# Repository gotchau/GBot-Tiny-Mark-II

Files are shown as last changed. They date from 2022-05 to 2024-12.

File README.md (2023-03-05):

# GBot-Tiny-Mark-II

<a href="https://discord.gg/KYU2nGtZ2r" style="height: 40px !important;">Join us on Discord</a>

Это вторая версия моего первого принтера GBot Tiny. Новый принтер теперь чуточку компактней по XY, но выше, при этом зона печати стала слегка больше.  

> [Список комплектующих для постройки принтера.](./docs/BOM_GBot_Tiny_Mark_II.md)

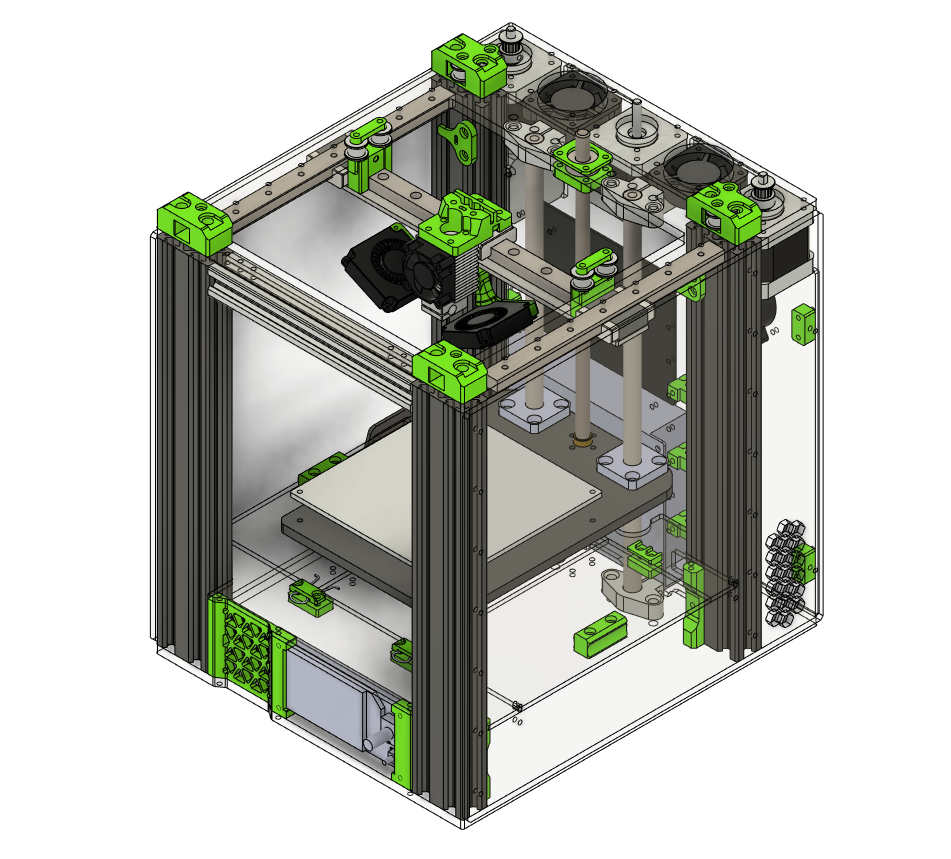
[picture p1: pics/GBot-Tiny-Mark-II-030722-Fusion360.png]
Внешний вид принтер


## Обзор конструкции
Рама теперь состоит из профиля 2040. Из-за того, что рама стала меньше, она стала жёстче. Первая версия не имела отсека под электронику, новая - целых два (легкодоступный под столиком и сзади). Материнскую плату и блок питания предполагается ставить сзади. Таким образом можно добиться максимально компактной компоновки и "подключать движки проводами 10см". Я для себя буду собирать принтер на клиппере, поэтому в переднем отсеке прекрасно разместится одноплатный компьютер со своим блоком питания или понижающим преобразователем.

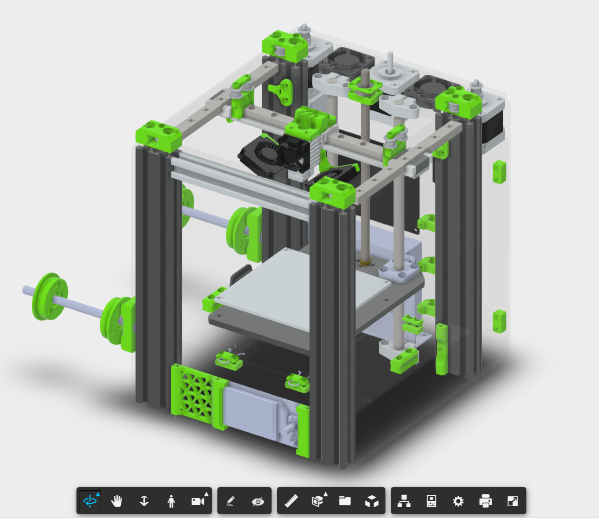
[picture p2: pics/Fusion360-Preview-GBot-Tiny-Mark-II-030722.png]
Preview (https://myhub.autodesk360.com/ue2ddbd59/shares/public/SH35dfcQT936092f0e43e492bbc572dd28c1?mode=embed)


> https://myhub.autodesk360.com/ue2ddbd59/g/shares/SH35dfcQT936092f0e43e492bbc572dd28c1?mode=embed

## Что изменилось?

- Рама стала жёстче
- Занимает меньше места на столе

- Появились отсеки для электроники (я говорил, что их два?)
- Каретки рельс не выходят за границы корпуса => корпус можно накрыть куполом и сделать пассивную термокамеру
- Концевики на датчиках Холла [А3144](./docs/Datasheet_A3144.pdf)
- Появилось нормальное крепление экрана (совмещено с подвальчиком)
- Появился подвальчик, доступ к которому есть сверху (принтер не требуется переворачивать)
- Катушка пластика меняется сверху, это позволяет ставить принтеры вплотную друг к другу
- Верхняя и нижняя плиты стали проще по геометрии, теоретически можно вырезать кустарно
- Рюкзак *aka* backpack/задний отсек имеет активное охлаждение (два осевых 4010, радиальный 4020)

## Примечание
В папке [CAD] вы найдёте актуальные модели для производства данного принтера. [DXF] - для лазерной резки, [STL] - для печати. В этих папках лежат детали с минимальным риском изменения. Остальные детали всегда можно взять из актуальной step-сборки принтера из папки [STEP].

Вся документация и вспомогательные файлы будут находиться здесь [docs].

[CAD]: ./CAD
[docs]: ./docs
[DXF]: ./CAD/Tiny%20Mark%20II/DXF
[STL]: ./CAD/Tiny%20Mark%20II/STL
[STEP]: ./CAD/Tiny%20Mark%20II/STEP

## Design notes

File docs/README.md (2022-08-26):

## Содержание данной секции:

**[BOM GBot Tiny Mark II.md](BOM_GBot_Tiny_Mark_II.md)** — список комплектующих

**[Fixings BOM GBot Tiny Mark II.md](Fixings_BOM_GBot_Tiny_Mark_II.md)** — расширенный список "болтов, винтов и гаек"

**[Datasheet A3144.pdf](Datasheet_A3144.pdf)** — документация на датчики Холла А3144, которые используются как концевики

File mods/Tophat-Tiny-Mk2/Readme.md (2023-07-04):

# Купол Tiny Mark II

## Внешний вид

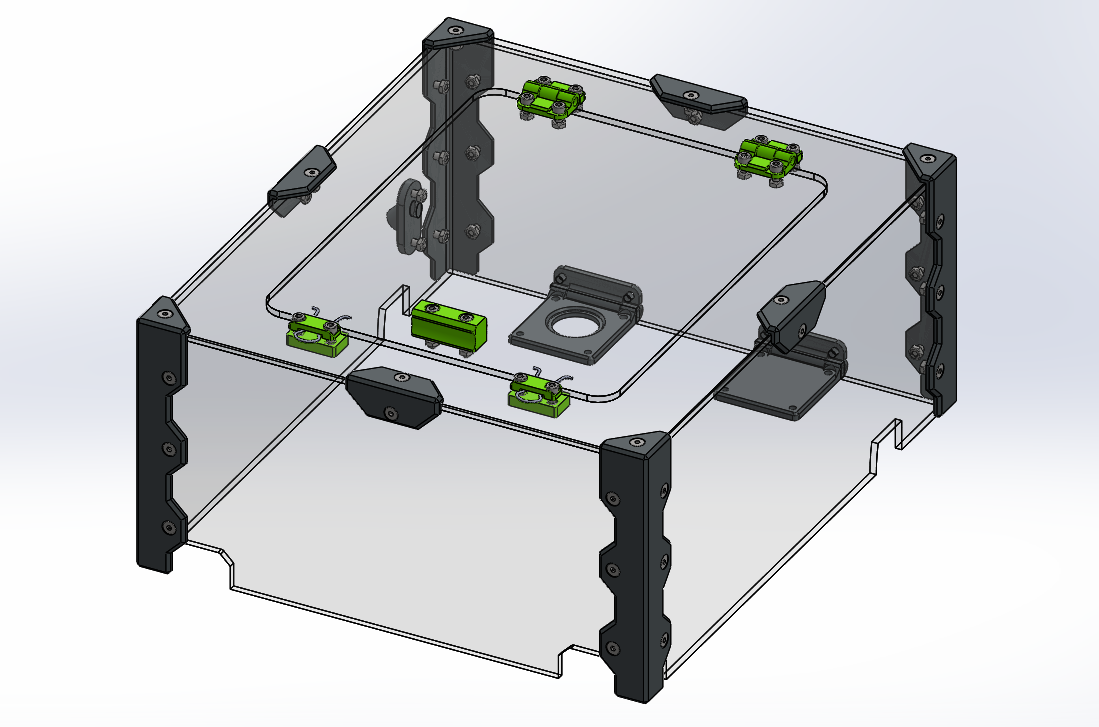
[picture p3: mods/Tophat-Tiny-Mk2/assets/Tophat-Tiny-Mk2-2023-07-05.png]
купол


Купол состоит из 5 панелей вырезанных из акрила 3мм, которые скрепляются с помощью печатных уголков. Пруток с пластиком заводится во внутрь по боудену через штуцер на боковой стенке. Жгут проводов до печатной головы идёт сквозь отверстие одной из петель. Спроектировано под разъем GX20. Петли крепятся на места вентиляторов отсека электроники. Отказ от них не критичен. У меня отсек работает всегда в пассивном режиме. 

Файлы STL и DXF находятся в соответствующих папках.

В папке **assets** есть несколько видео того, как это выглядит уже в собранном виде.

## Благодарности

Данный купол появился на свет благодаря активности сообщества. Большое спасибо Алексею.

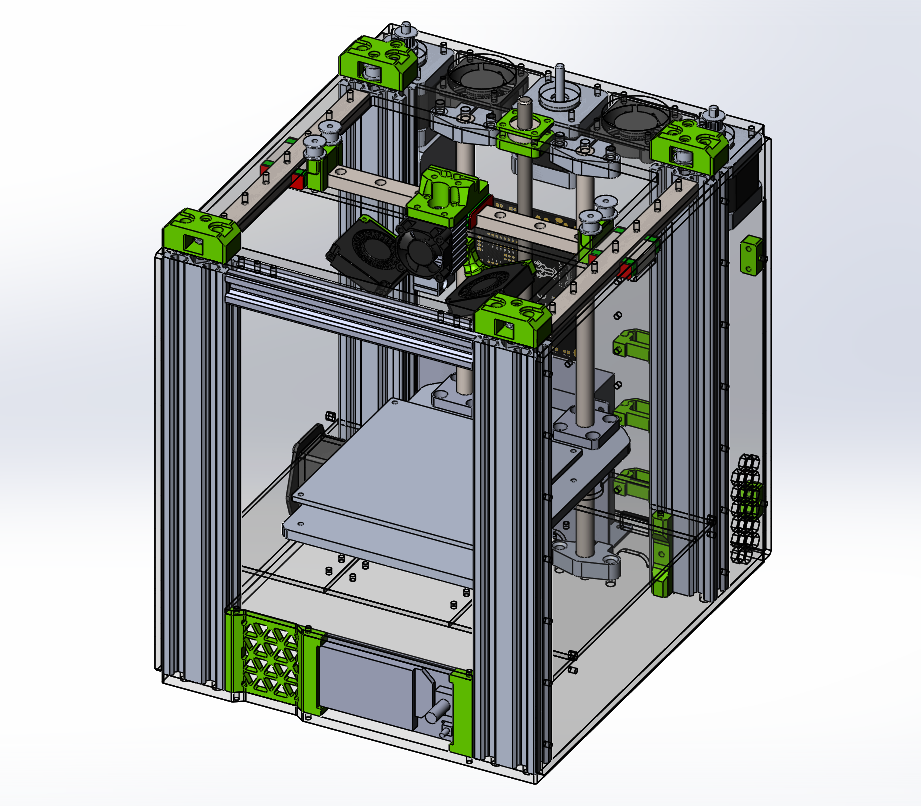
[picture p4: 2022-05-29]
pics/GBot-Tiny-Mark-II-290522.png

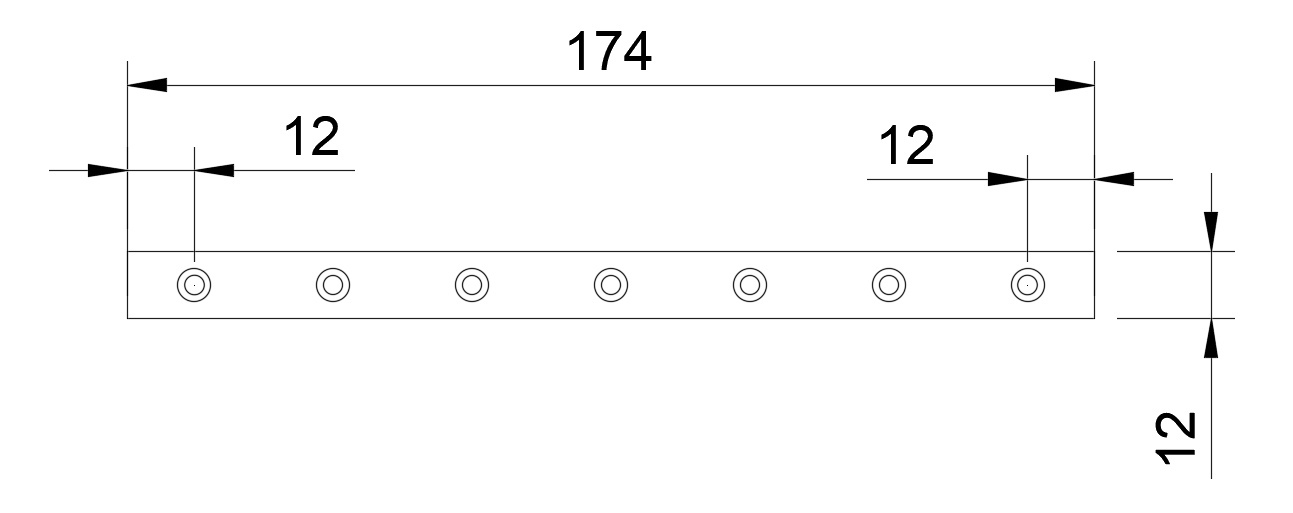
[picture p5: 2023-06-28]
docs/drawings/Y_Rail_GBot_Tiny_Mk2.jpg

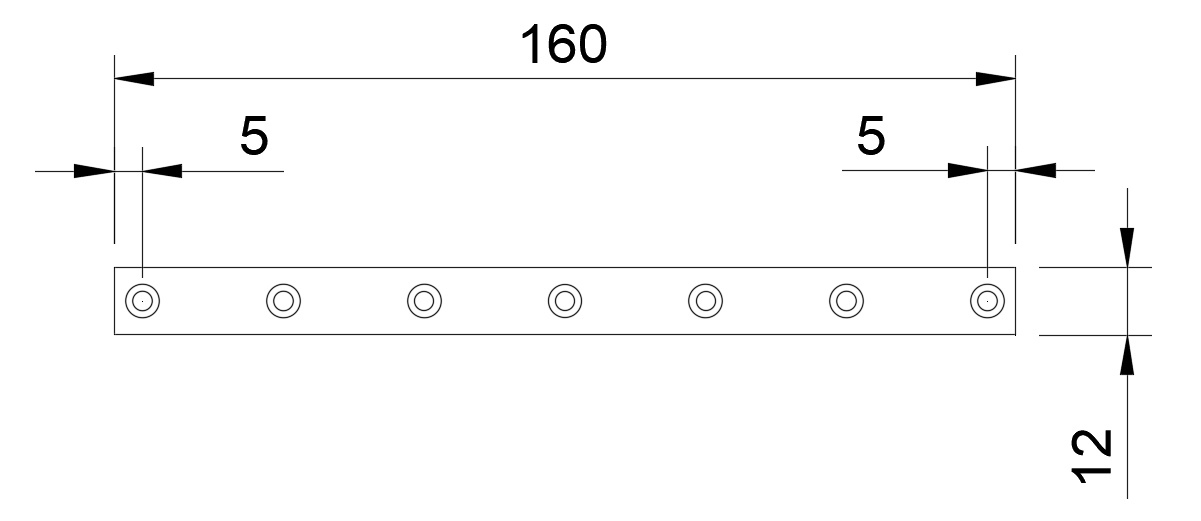
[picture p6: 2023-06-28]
docs/drawings/X_Rail_GBot_Tiny_Mk2.jpg

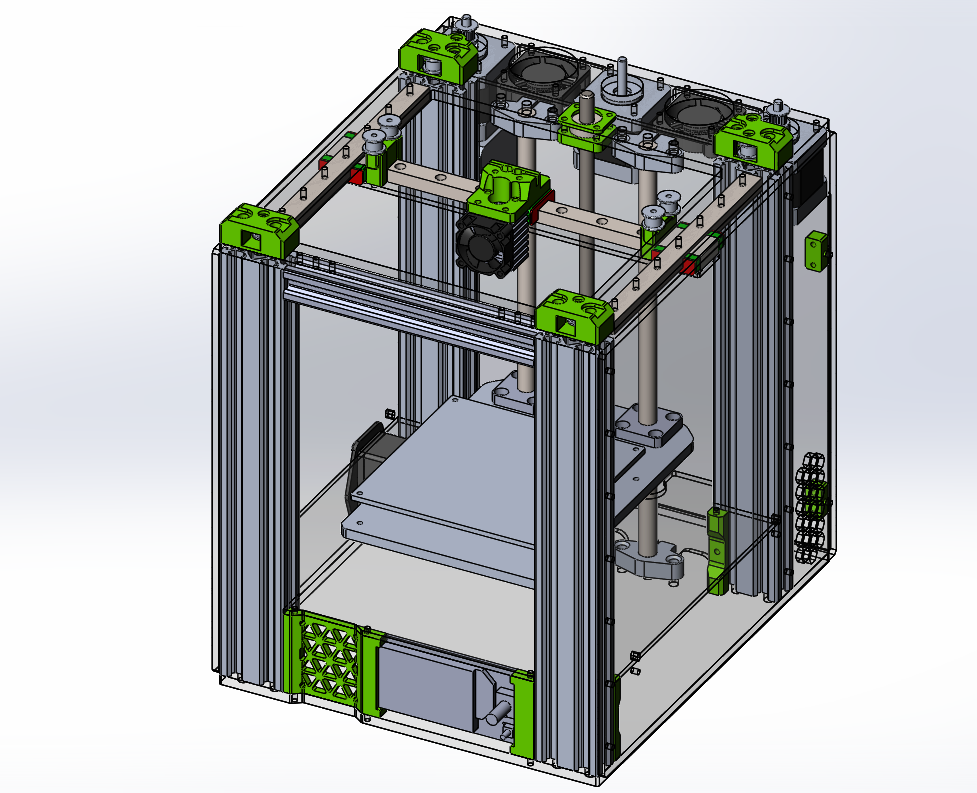
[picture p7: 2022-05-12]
pics/GBot-Tiny-Mark-II-120522.png

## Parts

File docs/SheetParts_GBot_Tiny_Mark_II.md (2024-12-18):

# Список листовых деталей

Несколько наименований в одной ячейке означает, что у детали есть несколько вариантов исполнения. Изготовить необходимо только одну.

## Акриловые детали для корпуса

| Название | Толщина | Количество | Комментарий |
| --- | :-----: | :---: | --- |
| topPlate GBtTinyMII.DXF |  6 мм | 1 | |
| bottomPlate GBtTinyMII.DXF<br/>bottomPlate 10mm GBtTinyMII.DXF |  6 мм | 1 | `bottomPlate 10mm` – отверстия для сквозной установки валов Z |
| leftPanel GBtTinyMII.DXF |  3 мм | 1 | |
| rightPanel GBtTinyMII.DXF |  3 мм | 1 | |
| electronicsCover GBtTinyMII.DXF |  3 мм | 1 | Комбинированная деталь<br/>Есть возможность вырезать по отдельности, детали с пометкой `(optional)`<br/>[Подробнее ниже](#electronicsCover-по-частям) |
| backPanel GBtTinyMII.DXF |  3 мм | 1 | |
| backBackPanel GBtTinyMII.DXF |  3 мм | 1 | |
| xRailSupport GBtTinyMII.DXF |  3 мм | 1 | |
| frontDoor GBtTinyMII.DXF | 3мм | 1 | Дверца (опция) |

## Прочие листовые детали

### Крепление стола

В таблице ниже представлено несколько вариаций крепления столика. Изготовить нужно только одну. Различия указаны в столбце комментарий.

Крепление стола по трём точкам предпочтительней. Если не знаете, что выбрать, берите `bedMount GBtTinyMII.DXF`. Материал сталь 4мм.

| Название | Толщина | Количество | Комментарий |
| --- | :-----: | :---: | --- |
| bedMount GBtTinyMII.DXF |  4 мм | 1 | Отверстия 3.5 мм под резьбу или рассверливание<br />Поддерживает крепление столика по 3 и 4 точкам |
| bedMount BH4 GBtTinyMII.DXF |  4 мм | 1 | Отверстия 4 мм сразу под винты М4<br />Поддерживает крепление столика по 3 и 4 точкам |
| bedMountThreePoint GBtTinyMII.DXF |  4 мм | 1 | Поддерживает крепление столика только 3 точкам |

### Пластина стола

Применяется для самостоятельной сборки столика, если его не удалось купить в сборе, так как с момента выхода принтера наблюдается дефицит столов 120мм. Снизу крепится грелка 100мм. Материал алюминий.

| Название | Толщина | Количество | Комментарий |
| --- | :-----: | :---: | --- |
| realHotBed 120x120mm.DXF |  3 мм | 1 | Поддерживает крепление по 3 и 4 точкам |

## electronicsCover по частям

Если вдруг материала не хватает, то electronicsCover можно вырезать частями.

| Название | Толщина | Количество | Комментарий |
| --- | :-----: | :---: | --- |
| (optional) back electronicsCover GBtTinyMII.DXF |  3 мм | 1 | |
| (optional) center electronicsCover GBtTinyMII.DXF |  3 мм | 1 | |
| (optional) front electronicsCover GBtTinyMII.DXF |  3 мм | 1 | |
| (optional) leftRight electronicsCover GBtTinyMII.DXF |  3 мм | 2 | |

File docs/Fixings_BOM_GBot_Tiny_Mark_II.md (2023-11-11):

# Список крепежа GBot Tiny Mark II

| Что | Сколько | Для чего | Комментарий |
| --- | --- | --- | --- |
| **Стенки** | | | |
| M3x8 | от 4 до 14 штук | Левая стенка | |
| M3x8 | от 4 до 14 штук | Правая стенка | |
| | | | |
| **Верхняя и нижняя пластины** | | | |
| M6x30 | 8 штук | Верхняя пластина | Силовые; DIN 912 |
| M6x20 | 8 штуки | Нижняя пластина | Силовые; DIN 912 |
| M3x12 | от 6 до 14 штук | Рельсы Y | |
| M3x12..18 | 6 штук | Холостые шкивы по периметру | |
| M3x20 | 8 штук | Вентиляторы заднего отсека | |
| M3x10 | 12 штук | Двигатели ABZ | |
| M3x12 | 4 штуки | Подшипник Z | |
| | | | |
| **Ось X** | | | |
| M3x40 | 4 штуки | Шкивы на оси Х | Рекомендуется винт с широкой шляпкой/фланцем;<br />DIN 967 или 7380-2 |
| M3x12 | 2 штуки | Флажок концевика Y | |
| M3x6 | 6 штук | Крепление поддержки рельсы оси Х | |
| M3x10 | от 3 до 7 штук  | Рельса оси Х | |
| | | | |
| **Ось Z** | | | |
| M5x20 | 8 штук | Валы оси Z | если валы с резьбой, то 4 штуки;<br />DIN 912 или DIN 7420 |
| M3x12 | 4 штуки | Латунная гайка | |
| M4x10 | 8 штук | Линейные подшипники | DIN 912 |
| | | | |
| **Печатная головка** | | | |
| M3x8 | 2 штуки | Крепление к каретке оси Х | |
| M3x18 | 2 штуки | Крепление к каретке оси Х | |
| M3x12 | 2 штуки | Крепление ремня | |
| M3x12 | 4 штуки | Крепление радиатора | |
| M3x16 | 2 штуки | Обдув модели | |
| M2x6..8 | 4 штуки | Обдув модели | |
| | | | |
| **Подвальчик** | | | |
| M3x16 | 4 штуки | Ручки крышки подвала | |
| M3x12 | 16 штук | Петли крышки подвала | |
| M3x12 | 8 штук | Защёлки/ответная часть | |
| M3x10 | 8 штук | Крепление к раме | |
| M3x10..20 | 6 штук | Крепление экрана | |
| M3x4 | 4 штуки | Крепление экрана | |
| M3x10 | 2 штуки | Гнездо питания | Рекомендуется DIN 965 |
| | | | |
| **Задний отсек электроники / рюкзак / backpack** | | | |
| M3x10 | 3 штуки | Блок питания | |
| M3x8 | 4 штуки | Шайбы упоры задней стенки электроники | |
| M3x12 | 9 штук | Крепление задней крышки | |
| M3x8 | 6 штук | Органайзер (если ставить 3 штуки) | |
| M3x8 | 8 штук | Крепление управляющей платы | Пластмассовые стойки |
| M3x8 | 4 штуки | Крепление управляющей платы | Пластмассовые винты |
| M3x8 | 4 штуки | Концевики YZ | |

*для большинства крепежа стоит брать DIN 7985 или 7380, если в таблице не указано иное

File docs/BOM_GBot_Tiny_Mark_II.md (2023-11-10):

# Список комплектующих GBot Tiny Mark II

### Железо

| Наименование | Количество | Ссылка | Комментарий |
| --- | :---: | --- | --- |
| Комплект шаговых двигателей | 1 | http://got.by/6eac1e | Всего требуется 4 двигателя<br />3 двигателя, если на директе |
| Рельс с кареткой MGN12C | 3 | http://got.by/6eac2d | Берём 200мм; Две для Y режутся в 174мм, одна для X 160мм |
| Блок питания Mean Well LRS-150-24 | 1 | http://got.by/6eac2y | |
| Печатающая головка | 1 | http://got.by/6eac44 | |
| Подающий механизм | 1 | http://got.by/6eac5o | В оригинале левое исполнение, но есть возможность собрать зеркально (с правым) |
| Вал 10мм (комплект из 2 шт) | 1 | http://got.by/6eac6u | Диаметр 10мм длина 300мм, режется в 270мм |
| Держатель вала SHF10 (комплект 4шт) | 1 | https://alii.pub/6lk0tg<br />https://alii.pub/6lk0v7 | |
| Линейный подшипник LMK10UU | 2 | http://got.by/6eacax | UU - короткий, LUU - длинный; нам нужен короткий |
| Шкивы на двигатели XY (16 зубов) | 2 | http://got.by/6eacca | 16 teeth bore 5 |
| Шкив на двигатель Z (20 зубов) | 1 | http://got.by/6eacca | 20 teeth bore 5 |
| Шкив на винт оси Z (20 зубов) | 1 | http://got.by/6eacca | 20 teeth bore 8 |
| Ремень резиновый армированный стекловолокном 2м | 1 | http://got.by/6eacd2 | 2M High Quality 6mm |
| Холостой шкив 16 зубов (без зубов) | 10 | http://got.by/6eacdg | 16T W6 B3 Without T |
| Кольцевой ремень GT2 122mm | 1 | http://got.by/6eacef | |
| Винт оси Z (шаг на свой вкус) | 1 | http://got.by/6eacfs | 250мм без крутилки, 300 если с ней |
| Подшипник 698zz (8x19x6) | 5 | http://got.by/6eacg6 | 1 на ось Z, еще 4 на ролики держателя катушки |
| Столик 120х120 | 1 | https://alii.pub/6lk13d<br />https://alii.pub/6lk16v<br />https://alii.pub/6lk18f<br />https://alii.pub/6lk1bx | |
| Пружинки стола (комплект 4шт) | 1 | https://alii.pub/6tke9z<br />https://alii.pub/6tkear | |
| Датчик Холла A3144 (комплект 10шт) | 1 | http://got.by/6em5eh | Используются как концевики; нужно только 3, по одному на ось |
| Магниты 3x2мм (комплект 10шт) | 1 | http://got.by/6ead34 | Требуются для концевиков; нужно только 3, по одному на ось |
| Гнездо питания AC-01A | 1 | http://got.by/6ead3w | |
| Турбинка 4010 24В | 2 | http://got.by/6ead52 | Обдув модели |
| Вентилятор 4010 24В | 2 | http://got.by/6ead52 | Вентиляция заднего отсека (стоят сверху) |
| Турбинка 4020 24В | 1 | https://alii.pub/6mvj2x | Прямой обдув драйверов или обдув модели на вулкане |
| Шаговый блинчик Nema14* | 1 | https://alii.pub/6k2ems | Если будете собирать на директе* |
| Комплект шестерней для директа* | 1 | https://alii.pub/6tkc5k<br />https://alii.pub/6tkc6x | Если будете собирать на директе* |

### Корпус

| Наименование | Количество | Ссылка | Комментарий |
| --- | :---: | --- | --- |
| Комплект акриловых деталей | 1 | https://vk.com/gotchaustuff<br />Discord: Gotchau#8053 | https://github.com/gotchau/GBot-Tiny-Mark-II/tree/main/CAD/DXF<br />* В папке могут быть не все детали, на всякий случай сверяйтесь с актуальной версией STEP сборки |
| Коплект печатных деталей | 1 | https://vk.com/gotchaustuff<br />Discord: Gotchau#8053 | https://github.com/gotchau/GBot-Tiny-Mark-II/tree/main/CAD/STL<br />* В папке могут быть не все детали, на всякий случай сверяйтесь с актуальной версией STEP сборки |
| Профиль V-slot 2040 (комплект + резка) | 1 | [https://www.soberizavod.ru](https://www.soberizavod.ru/) | 270мм х4 |
| Профиль V-slot 2020 (комплект + резка) | 1 | [https://www.soberizavod.ru](https://www.soberizavod.ru/) | 155мм х1; опционален, можно собрать без него |

### Электроника

| Наименование | Количество | Ссылка | Комментарий |
| :--- | :---: | --- | --- |
| Плата управления BIGTREETECH  SKR 3 (With TMC2209x5) | 1 | http://got.by/6eadbh | Марлин; <br />для Клиппера нужен любой одноплатник |
| или | | | |
| Плата управления Mellow Fly Gemini V3 (With 2209) | 1 | https://alii.pub/6mvilm | Клиппер (имеет на борту одноплатник) |
| Экран BIGTREETECH  Mini12864 | 1 | http://got.by/6eadc2 | |
| Провод EXP1/EXP2 для экрана 50см (пара) | 1 | https://vk.com/gotchaustuff<br />Discord: Gotchau#8053 | |

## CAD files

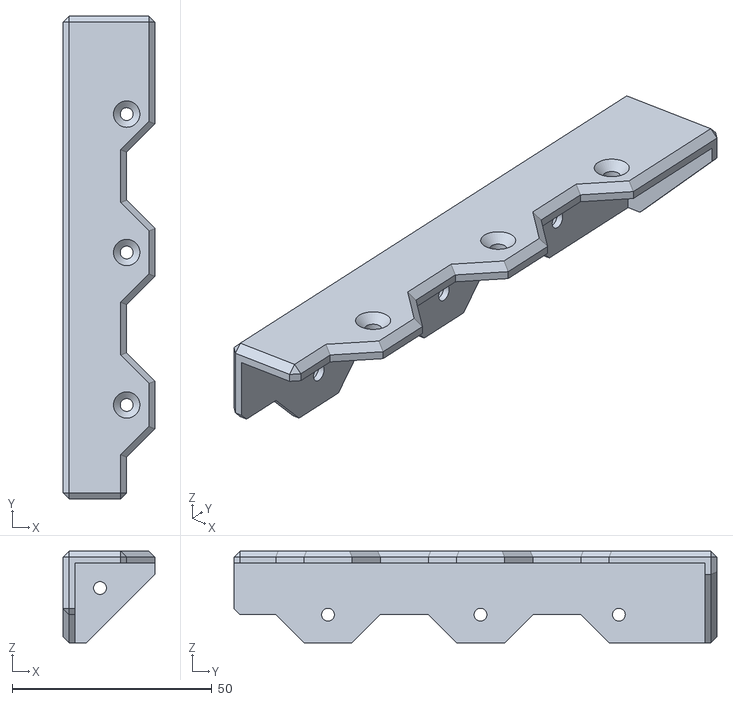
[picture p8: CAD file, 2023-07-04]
mods/Tophat-Tiny-Mk2/STL/cornerMain-TophatTinyMk2.STL
23.0 x 120.8 x 23.0

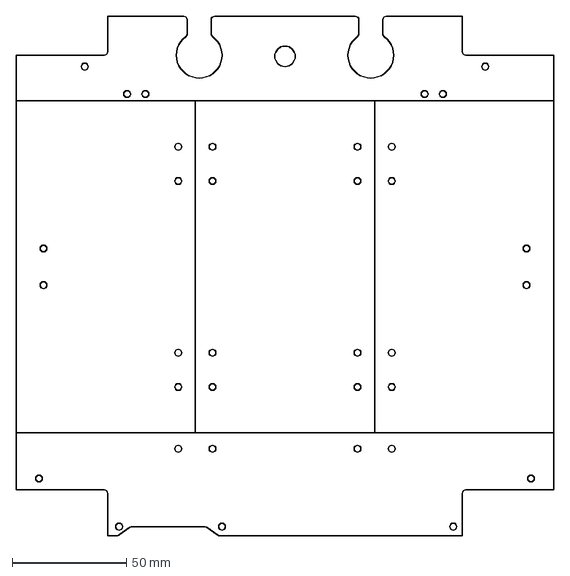
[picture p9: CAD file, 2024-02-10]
CAD/Tiny Mark II/DXF/electronicsCover GBtTinyMII.DXF
235.0 x 227.0 mm

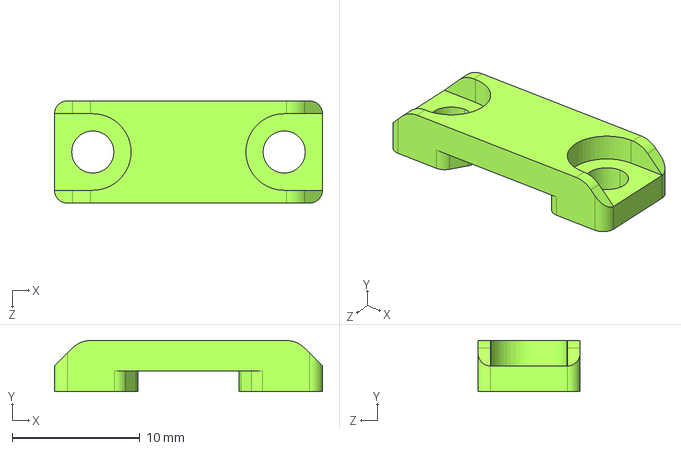
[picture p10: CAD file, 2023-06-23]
CAD/Tiny Mark II/STEP/latchHousing.STEP
21.0 x 4.00 x 8.00 mm

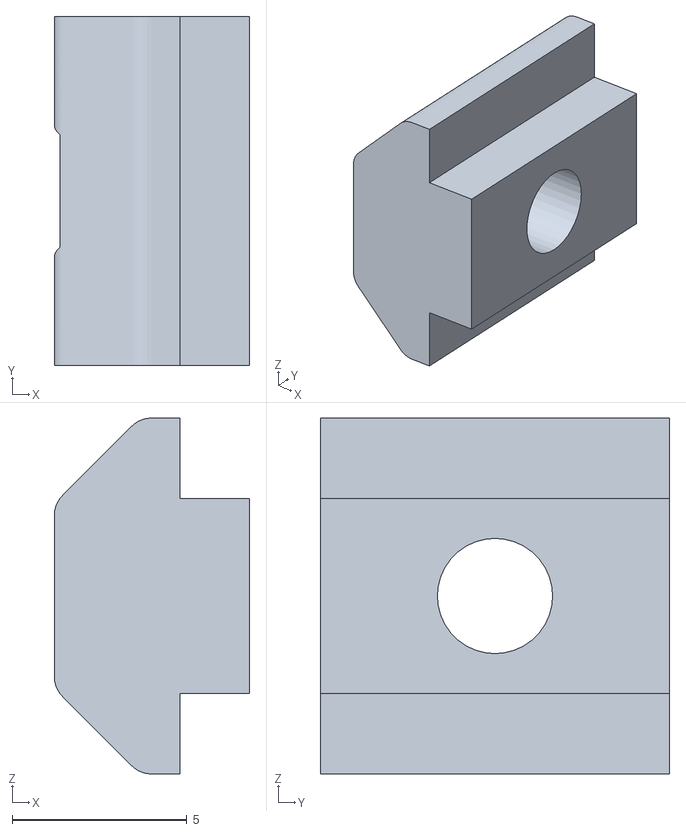
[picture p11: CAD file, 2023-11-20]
CAD/Tiny Mark II/STL/justOneNut.STL
5.60 x 10.0 x 10.2

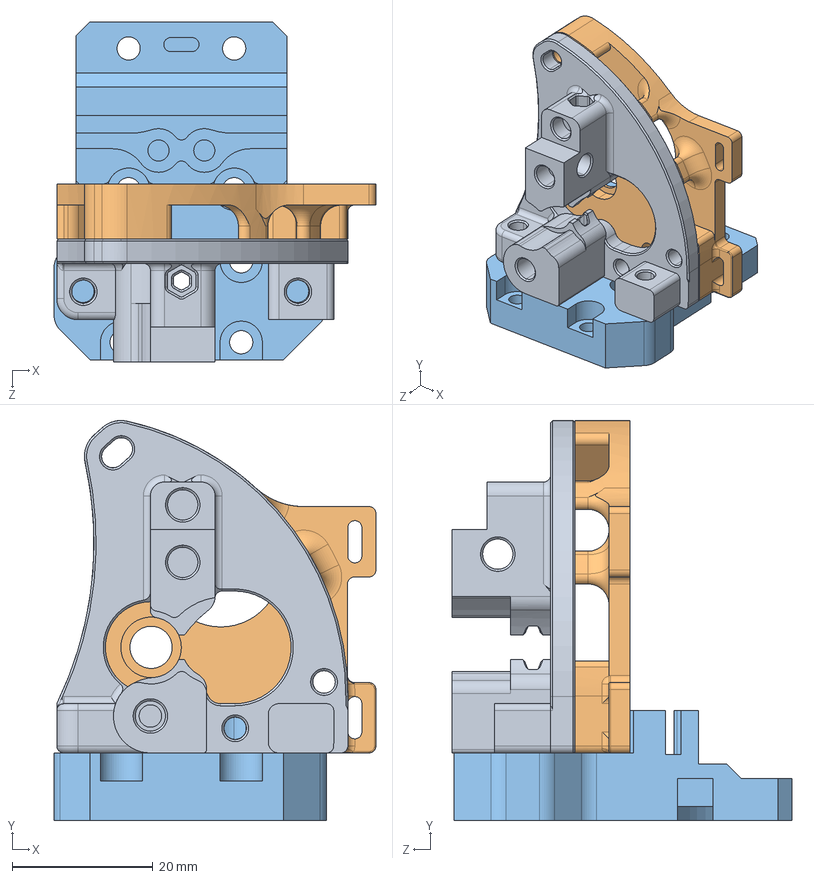
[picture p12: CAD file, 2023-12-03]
CAD/TinySailfin/STEP/TinySailfin.STEP
45.7 x 56.8 x 48.3 mm
mid Mod GotchauSailfin
back Mod GotchauSailfin
printHeadMount Mod GBtTinyMII GotchauSailfin

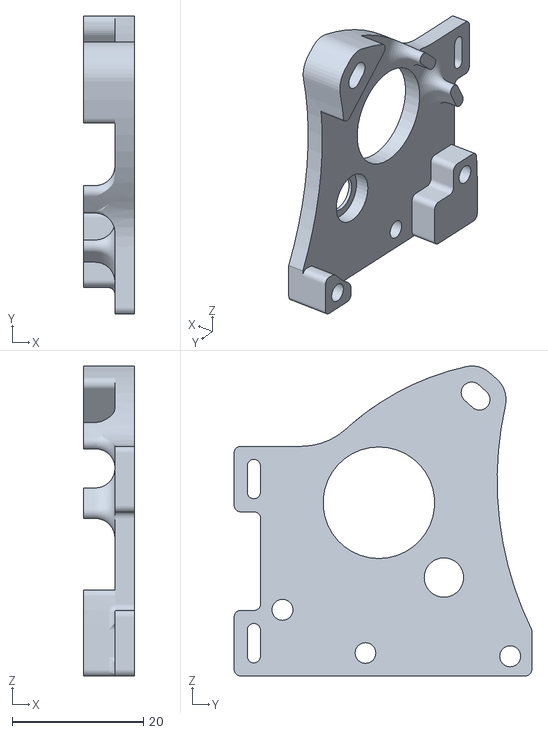
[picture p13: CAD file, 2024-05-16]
CAD/TinySailfin/STL/Back2 TinySailfin.STL
7.80 x 45.4 x 47.2

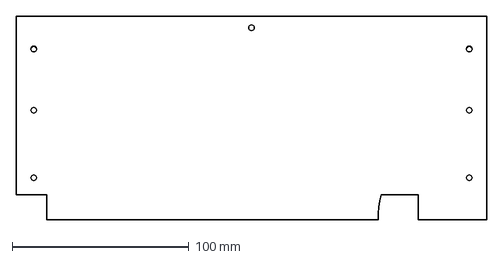
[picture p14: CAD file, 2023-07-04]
mods/Tophat-Tiny-Mk2/DXF/rightPanel-TophatTinyMk2.DXF
266.0 x 115.0 mm

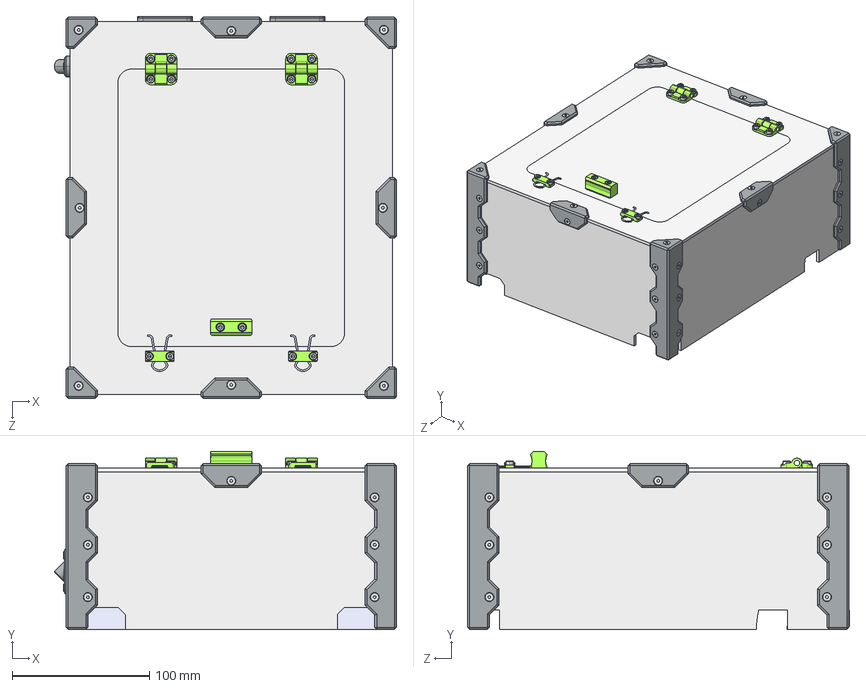
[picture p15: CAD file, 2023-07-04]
mods/Tophat-Tiny-Mk2/STEP/Tophat-Tiny-Mk2.STEP
249.4 x 130.0 x 278.5 mm
latch^latchAsm_Tophat-Tiny-Mk2 x 2
latchHousing^latchAsm_Tophat-Tiny-Mk2 x 2
backPanel TophatTinyMk2^Tophat-Tiny-Mk2
frontPanel TophatTinyMk2^Tophat-Tiny-Mk2
rightPanel TophatTinyMk2^Tophat-Tiny-Mk2
leftPanel TophatTinyMk2^Tophat-Tiny-Mk2
topPanel TophatTinyMk2^Tophat-Tiny-Mk2
cornerMain TophatTinyMk2^Tophat-Tiny-Mk2 x 4
cornerSubside TophatTinyMk2^Tophat-Tiny-Mk2 x 4
electronicsCoverHingeT3 GBtTinyMII^Tophat-Tiny-Mk2 x 2
electronicsCoverBottomLatchPart GBtTinyMII^Tophat-Tiny-Mk2 x 2
electronicsCoverHandle GBtTinyMII^Tophat-Tiny-Mk2
hingeBlank TophatTinyMk2^Tophat-Tiny-Mk2
hingeCircleCut TophatTinyMk2^Tophat-Tiny-Mk2
ISO 4762 - M3 x 8^Tophat-Tiny-Mk2 x 8
ISO 4032 - M3^Tophat-Tiny-Mk2 x 19
ISO 4762 - M3 x 10^Tophat-Tiny-Mk2 x 4
ISO 4762 - M3 x 16^Tophat-Tiny-Mk2 x 2
ISO 4032 - M3_1^Tophat-Tiny-Mk2 x 39
DIN 7991 - M3x8^Tophat-Tiny-Mk2 x 36
bowdenGuide TophatTinyMk2^Tophat-Tiny-Mk2
ISO 4762 - M3 x 8_1^Tophat-Tiny-Mk2 x 2

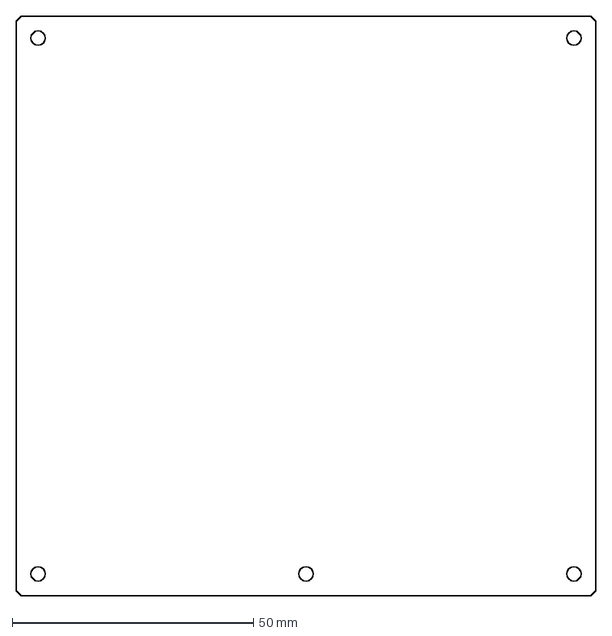
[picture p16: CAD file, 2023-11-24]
CAD/Tiny Mark II/DXF/realHotBed 120x120mm.DXF
120.0 x 120.0 mm

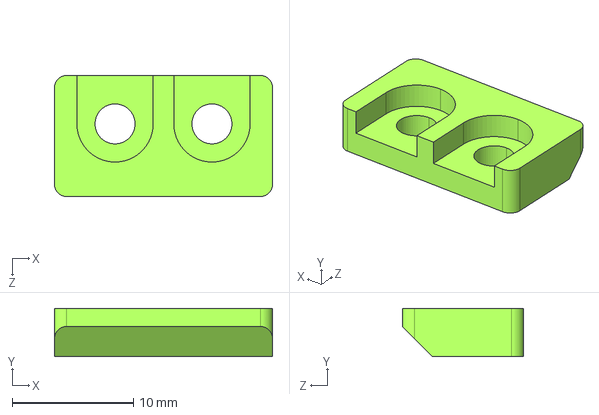
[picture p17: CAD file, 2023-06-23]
CAD/Tiny Mark II/STEP/electronicsCoverTopPseudoHinge GBtTinyMII.STEP
18.0 x 4.00 x 10.0 mm

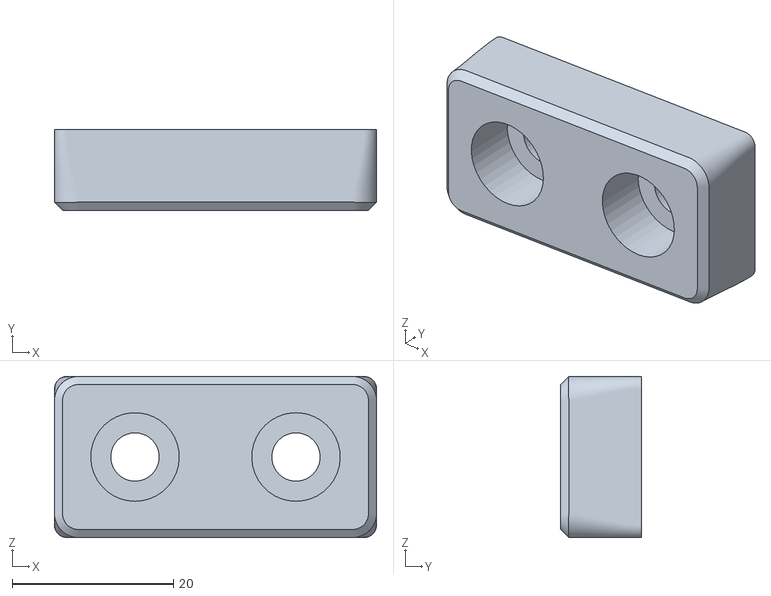
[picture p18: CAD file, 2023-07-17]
CAD/Tiny Mark II/STL/foot GBtTinyMII.STL
40.0 x 10.00 x 20.0

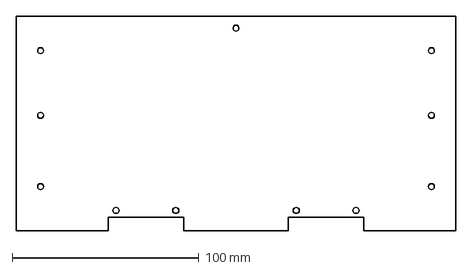
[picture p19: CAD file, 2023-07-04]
mods/Tophat-Tiny-Mk2/DXF/backPanel-TophatTinyMk2.DXF
235.0 x 115.0 mm

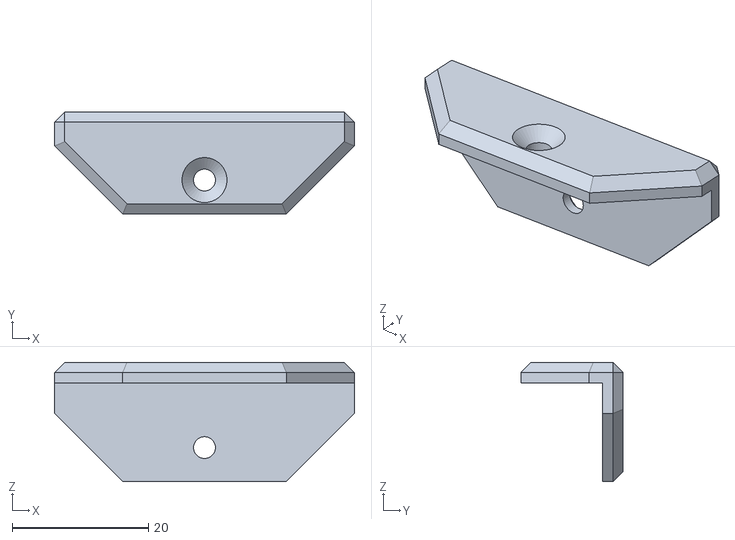
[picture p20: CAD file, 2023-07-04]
mods/Tophat-Tiny-Mk2/STL/cornerSubside-TophatTinyMk2.STL
44.0 x 15.0 x 17.5

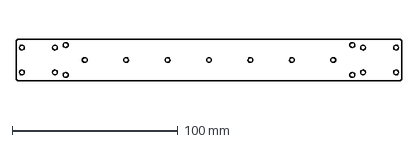
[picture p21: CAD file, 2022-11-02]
CAD/Tiny Mark II/DXF/xRailSupport GBtTinyMII.DXF
233.0 x 25.0 mm

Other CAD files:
CAD/TinySailfin/STEP/back Mod GotchauSailfin.STEP
CAD/Tiny Mark II/STEP/doorHingeP1 GBtTinyMII.STEP
CAD/Tiny Mark II/STL/zOpticEndstopMount GBtTinyMII.STL
CAD/TinySailfin/STEP/mid Mod GotchauSailfin.STEP
CAD/Tiny Mark II/DXF/(optional) back electronicsCover GBtTinyMII.DXF
CAD/Tiny Mark II/DXF/(optional) center electronicsCover GBtTinyMII.DXF
CAD/Tiny Mark II/DXF/(optional) front electronicsCover GBtTinyMII.DXF
CAD/Tiny Mark II/DXF/(optional) leftRight electronicsCover GBtTinyMII.DXF
CAD/Tiny Mark II/DXF/backBackPanel GBtTinyMII.DXF
CAD/Tiny Mark II/DXF/backPanel GBtTinyMII.DXF
CAD/Tiny Mark II/DXF/bedMount BH4 GBtTinyMII.DXF
CAD/Tiny Mark II/DXF/bedMount GBtTinyMII.DXF
CAD/Tiny Mark II/DXF/bedMountThreePoint GBtTinyMII.DXF
CAD/Tiny Mark II/DXF/bottomPlate 10mm GBtTinyMII.DXF
CAD/Tiny Mark II/DXF/bottomPlate GBtTinyMII.DXF
CAD/Tiny Mark II/DXF/frontDoor GBtTinyMII.DXF
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

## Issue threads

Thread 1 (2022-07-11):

Ошибочная ссылка на датчики холла

UndeadMorose, 2022-07-11:
https://github.com/gotchau/GBot-Tiny-Mark-II/blob/0d5c3992c686f5f158b14fd9a77022753a712945/docs/BOM_GBot_Tiny_Mark_II.md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
В описании ссылка на датчики холла некорректна (равна ссылке на Столик 120х120)

gotchau, 2022-07-17:
Ссылка исправлена. Спасибо

Closed 2022-07-17.

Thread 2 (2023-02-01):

Old link in BOM (01.02.2023)

UndeadMorose, 2023-02-01:
Невозможно купить по ссылке | Can't buy from link
https://github.com/gotchau/GBot-Tiny-Mark-II/blob/6027beb782a5f8fa3919d7d40bc652ea41d21398/docs/BOM_GBot_Tiny_Mark_II.md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
https://github.com/gotchau/GBot-Tiny-Mark-II/blob/6027beb782a5f8fa3919d7d40bc652ea41d21398/docs/BOM_GBot_Tiny_Mark_II.md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

gotchau, 2023-02-02:
Ссылки обновлены и на всякий случай продублированы

Closed 2023-02-04.

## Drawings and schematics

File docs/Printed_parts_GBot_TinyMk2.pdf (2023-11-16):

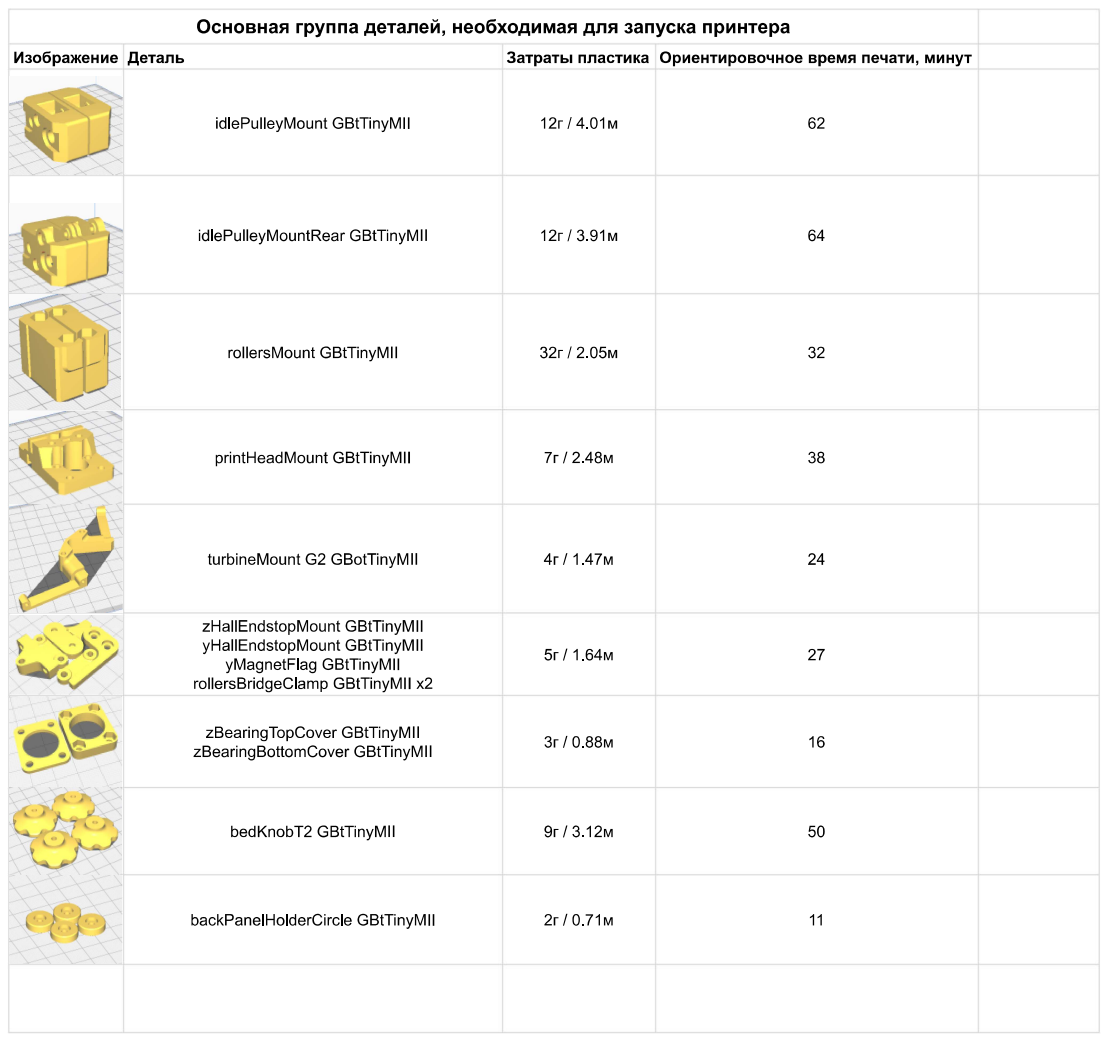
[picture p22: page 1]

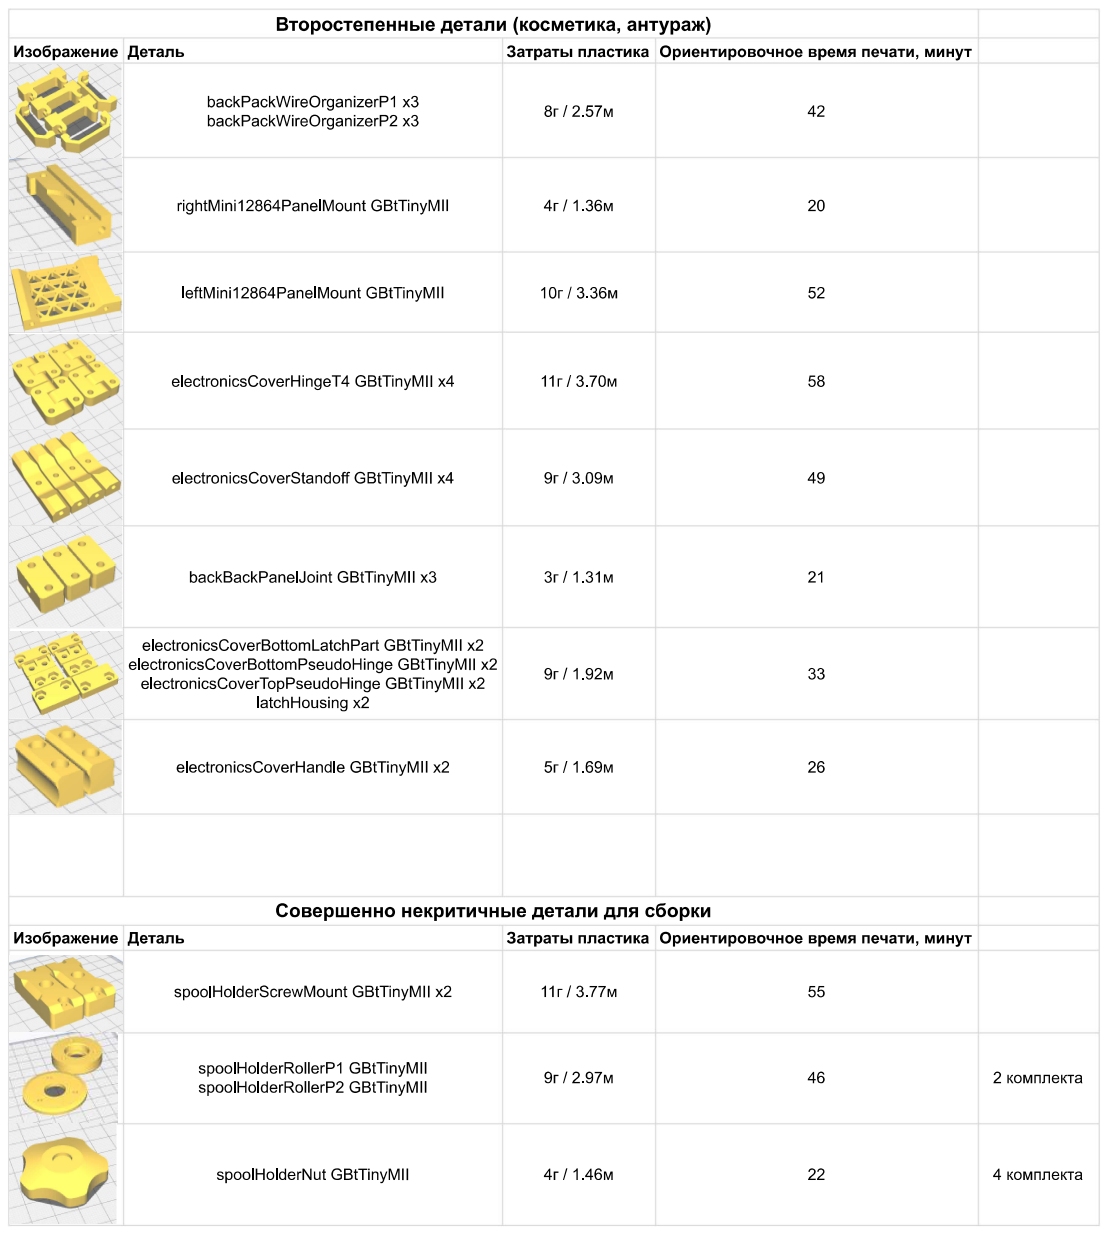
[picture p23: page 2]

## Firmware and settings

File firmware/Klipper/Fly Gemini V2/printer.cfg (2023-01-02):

[include fly_macros.cfg]

########################################
# Motherboard model
# Please modify it based on your motherboard model
# 请根据您的主板型号修改
########################################
#[include boards/FLY_GEMINI_V1.cfg]
#[include boards/FLY_GEMINI_V1.1.cfg]
[include boards/FLY_GEMINI_V2.cfg]


[mcu]
serial: /dev/ttyACM0

[mcu host]
serial: /tmp/klipper_host_mcu

[virtual_sdcard]
path: ~/gcode_files

[printer]
kinematics: corexy
max_velocity: 300
max_accel: 3000
max_z_velocity: 5
max_z_accel: 100


########################################
# Temp
########################################
[temperature_sensor Host]
sensor_type: temperature_host


########################################
# Drives
########################################
[stepper_x]
step_pin: X_STEP
dir_pin: X_DIR
enable_pin: !X_EN
microsteps: 16
rotation_distance: 32
endstop_pin: !X_STOP
position_endstop: 0
position_max: 120
homing_speed: 25

[stepper_y]
step_pin: Y_STEP
dir_pin: Y_DIR
enable_pin: !Y_EN
microsteps: 16
rotation_distance: 32
endstop_pin: !Y_STOP
position_endstop: 113
position_max: 113
homing_speed: 25

[stepper_z]
step_pin: Z_STEP
dir_pin: Z_DIR
enable_pin: !Z_EN
microsteps: 16
rotation_distance: 2
endstop_pin: !Z_STOP
position_endstop: 0
position_max: 80
homing_speed: 10

[extruder]
step_pin: E_STEP
dir_pin: E_DIR
enable_pin: !E_EN
microsteps: 16
rotation_distance: 23.55
gear_ratio: 50:10
nozzle_diameter: 0.400
filament_diameter: 1.750
heater_pin: HEAT
sensor_pin: HEAT_TEMP
sensor_type: ATC Semitec 104GT-2
max_power: 0.3
control: pid
pid_Kp: 22.2
pid_Ki: 1.08
pid_Kd: 114
min_temp: 0
max_temp: 260


########################################
# BED
########################################
[heater_bed]
heater_pin: BED_OUT
sensor_pin: BED_TEMP
sensor_type: Generic 3950
max_power: 0.3
control = pid
pid_kp = 17.373
pid_ki = 1.103
pid_kd = 68.406
pwm_cycle_time: 0.050
min_temp: 0
max_temp: 130


########################################
# FANs
########################################
[fan]
pin: FAN0

[heater_fan fan1]
pin: FAN1
max_power:0.3
cycle_time: 0.005
shutdown_speed:0


########################################
# TMC2209 configuration
########################################
[tmc2209 stepper_x]
uart_pin: X_CS
run_current: 0.900
stealthchop_threshold: 250

[tmc2209 stepper_y]
uart_pin: Y_CS
run_current: 0.900
stealthchop_threshold: 250

[tmc2209 stepper_z]
uart_pin: Z_CS
run_current: 0.500
stealthchop_threshold: 250

[tmc2208 extruder]
uart_pin: E_CS
run_current: 0.200
stealthchop_threshold: 250


#######################################
# Mini 12864 LCD
#######################################
[display]
lcd_type: uc1701
cs_pin: EXP1_3
a0_pin: EXP1_4
rst_pin: EXP1_5
contrast: 63
encoder_pins: ^EXP2_5, ^!EXP2_3
click_pin: ^!EXP1_2
#spi_bus: spi1

[neopixel mini12864]
pin: EXP1_6
chain_count: 3
initial_RED: 0.9
initial_GREEN: 0.4
initial_BLUE: 0.0
color_order: RGB

[neopixel case]
pin: PB0
chain_count: 18
color_order: GRB
initial_RED: 0.2
initial_GREEN: 0.2
initial_BLUE: 0.2

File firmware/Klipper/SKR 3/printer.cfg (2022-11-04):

#Конфигурационный файл GBot Tiny Mark II
#Плата BTT SKR 3
#Кинематика hbot
#Gotchau 24.06.22

[stepper_x]
step_pin: PD4
dir_pin: PD3
enable_pin: !PD6
microsteps: 16
rotation_distance: 32
endstop_pin: !PC1
position_endstop: 0
position_max: 120
homing_speed: 25

[stepper_y]
step_pin: PA15
dir_pin: PA8
enable_pin: !PD1
microsteps: 16
rotation_distance: 32
endstop_pin: ^!PC3
position_endstop: 110
position_max: 110
homing_speed: 25

[stepper_z]
step_pin: PE2
dir_pin: PE3
enable_pin: !PE0
microsteps: 16
rotation_distance: 8
endstop_pin: !PC0
position_endstop: 0
position_max: 80
homing_speed: 10

[extruder]
step_pin: PD15
dir_pin: PD14
enable_pin: !PC7
microsteps: 16
rotation_distance: 33.500
nozzle_diameter: 0.400
filament_diameter: 1.750
heater_pin: PB3
sensor_type: EPCOS 100K B57560G104F
sensor_pin: PA2
control: pid
pid_kp = 24.769
pid_ki = 1.635
pid_kd = 93.813
min_temp: 0
max_temp: 250

[heater_bed]
heater_pin: PD7
sensor_type: Generic 3950
sensor_pin: PA1
max_power: 0.3
control: pid
pid_kp = 18.538
pid_ki = 1.315
pid_kd = 65.347
pwm_cycle_time: 0.050
min_temp: 0
max_temp: 130

[heater_fan fan1]
pin: PB5

[fan]
pin: PB6

[fan_generic fan]
pin: PB7

[mcu]
serial: /dev/serial/by-id/usb-Klipper_stm32h743xx_46002E001651303230343132-if00
restart_method: command

[printer]
kinematics: corexy
max_velocity: 300
max_accel: 3000
max_z_velocity: 25
max_z_accel: 100

[temperature_sensor host]
sensor_type: temperature_host

########################################
# EXP1 / EXP2 (display) pins
########################################

[board_pins]
aliases:
    # EXP1 header
    EXP1_1=PC5, EXP1_3=PB1, EXP1_5=PE9,  EXP1_7=PE11, EXP1_9=<GND>,
    EXP1_2=PB0, EXP1_4=PE8, EXP1_6=PE10, EXP1_8=PE12, EXP1_10=<5V>,
    # EXP2 header
    EXP2_1=PA6, EXP2_3=PE7, EXP2_5=PB2, EXP2_7=PC4,   EXP2_9=<GND>,
    EXP2_2=PA5, EXP2_4=PA4, EXP2_6=PA7, EXP2_8=<RST>, EXP2_10=<NC>

######################################################################
# MiniPanel12864 (with neopixel backlight leds)
######################################################################
[display]
lcd_type: uc1701
cs_pin: EXP1_3
a0_pin: EXP1_4
rst_pin: EXP1_5
contrast: 63
encoder_pins: ^EXP2_5, ^EXP2_3
click_pin: ^!EXP1_2
spi_software_miso_pin: EXP2_1
spi_software_mosi_pin: EXP2_6
spi_software_sclk_pin: EXP2_2

[output_pin beeper]
pin: EXP1_1
pwm: True
value: 0
shutdown_value: 0
cycle_time: 0.0002

[neopixel mini12864]
pin: EXP1_6
chain_count: 3
color_order: BRG
initial_RED: 0.6
initial_GREEN: 0.0
initial_BLUE: 1.0

[neopixel case]
pin: PE6
chain_count: 18
color_order: GRB
initial_RED: 0.2
initial_GREEN: 0.2
initial_BLUE: 0.2

# [delayed_gcode lights]
# initial_duration: 1.
# gcode:
#   SET_LED LED=mini12864 RED=0.0 GREEN=0.0 BLUE=0.0 INDEX=1 TRANSMIT=1
#   SET_LED LED=mini12864 RED=0.6 GREEN=0.0 BLUE=1.0 INDEX=2 TRANSMIT=1
#   SET_LED LED=mini12864 RED=0.0 GREEN=0.0 BLUE=0.0 INDEX=3 TRANSMIT=1

########################################
# TMC2209 configuration
########################################

[tmc2209 stepper_x]
uart_pin: PD5
run_current: 0.800
stealthchop_threshold: 200

[tmc2209 stepper_y]
uart_pin: PD0
run_current: 0.800
stealthchop_threshold: 200

[tmc2209 stepper_z]
uart_pin: PE1
run_current: 0.300
stealthchop_threshold: 200

[tmc2209 extruder]
uart_pin: PC6
run_current: 0.800
stealthchop_threshold: 200

[virtual_sdcard]
path: ~/gcode_files

[display_status]

[pause_resume]

[include macro.cfg]

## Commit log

2022-05-13 Update topPlate GBtTinyMII.DXF
    [topPlate GBtTinyMII.DXF]
2022-05-14 some panels added
    [backBackPanel GBtTinyMII.DXF, electronicsCover GBtTinyMII.DXF]
2022-05-16 Create BOM GBot Tiny Mark II.xlsx
    [BOM GBot Tiny Mark II.xlsx]
2022-05-16 Update BOM GBot Tiny Mark II.xlsx
    [BOM GBot Tiny Mark II.xlsx]
2022-05-21 files added
    [electronicsCoverHinge GBtTinyMII.STL]
2022-06-08 dxfs upd
    [backBackPanel GBtTinyMII.DXF, backPanel GBtTinyMII.DXF, bottomPlate GBtTinyMII.DXF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]
2022-06-15 optional electronicsCover pieces
    [(optional) back electronicsCover GBtTinyMII.DXF, (optional) center electronicsCover GBtTinyMII.DXF, (optional) front electronicsCover GBtTinyMII.DXF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]
2022-07-07 md BOM added
    [BOM GBot Tiny Mark II.xlsx]
2022-07-09 steps added
    [backBackPanel GBtTinyMII.STEP, backPanel GBtTinyMII.STEP, bedMount GBtTinyMII.STEP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]
2022-08-05 Update bedMount GBtTinyMII.DXF
    [bedMount GBtTinyMII.DXF]
2022-08-08 DXF updated
    [backPanel GBtTinyMII.DXF, bedMount GBtTinyMII.DXF, bottomPlate 10mm GBtTinyMII.DXF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]
2022-08-08 Klipper config added
    config for SKR3
    [macro.cfg, printer.cfg]
2022-08-11 a lot of stuff added
    [backBackPanelJoint GBtTinyMII.STL, backPackWireOrganizerP1.STL, backPackWireOrganizerP2.STL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]
2022-09-14 bedMount fix
    [bedMount BH4 GBtTinyMII.DXF, bedMount GBtTinyMII.DXF]
2022-09-14 bed fix upd
    [bedMount BH4mm GBtTinyMII.dxf, bedMountThreePoint GBtTinyMII.DXF]
2022-11-02 Tiny Sailfin
    [(optional) back electronicsCover GBtTinyMII.DXF, (optional) center electronicsCover GBtTinyMII.DXF, (optional) front electronicsCover GBtTinyMII.DXF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]
2022-11-02 Create screwKnob TinySailfin.STL
    [screwKnob TinySailfin.STL]
2023-02-17 door parts added
    [doorHandle GBtTinyMII.STL, doorHandleStop GBtTinyMII.STL, doorHingeP1 GBtTinyMII.STL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]
2023-05-08 Create printHeadMount Mod GBtTinyMII GotchauSailfin.STEP
    [printHeadMount Mod GBtTinyMII GotchauSailfin.STEP]
2023-11-24 Create realHotBed 120x120mm.DXF
    [realHotBed 120x120mm.DXF]
2024-02-10 Update electronicsCover GBtTinyMII.DXF
    [electronicsCover GBtTinyMII.DXF]
2024-05-16 Create Back2 TinySailfin.STL
    [Back2 TinySailfin.STL]
